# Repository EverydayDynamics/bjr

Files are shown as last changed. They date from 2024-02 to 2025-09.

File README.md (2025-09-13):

# bjr
A Ball Juggling Robot's repository

## Getting started

### firmware build and flashing

install rust on you computer
```
curl --proto '=https' --tlsv1.2 -sSf https://sh.rustup.rs | sh
```
Install the target toolchain

```
rustup target add thumbv7em-none-eabihf
```

Install probe-rs
```
curl --proto '=https' --tlsv1.2 -LsSf https://github.com/probe-rs/probe-rs/releases/latest/download/probe-rs-tools-installer.sh | sh
```
Download and install jlink tools from here
https://www.segger.com/downloads/jlink/
Restart your shell
Change directory to the main software
```
cd software/central_control_firmware
```

Build the firmware with:
```
cargo embed --bin main_app --release 
```
### telemetry visualizer build
Change directory to the visualizer
```
cd software/telemetry_visualizer
```

Build the visualizer with:
```
cargo embed --bin main_app --release 
```

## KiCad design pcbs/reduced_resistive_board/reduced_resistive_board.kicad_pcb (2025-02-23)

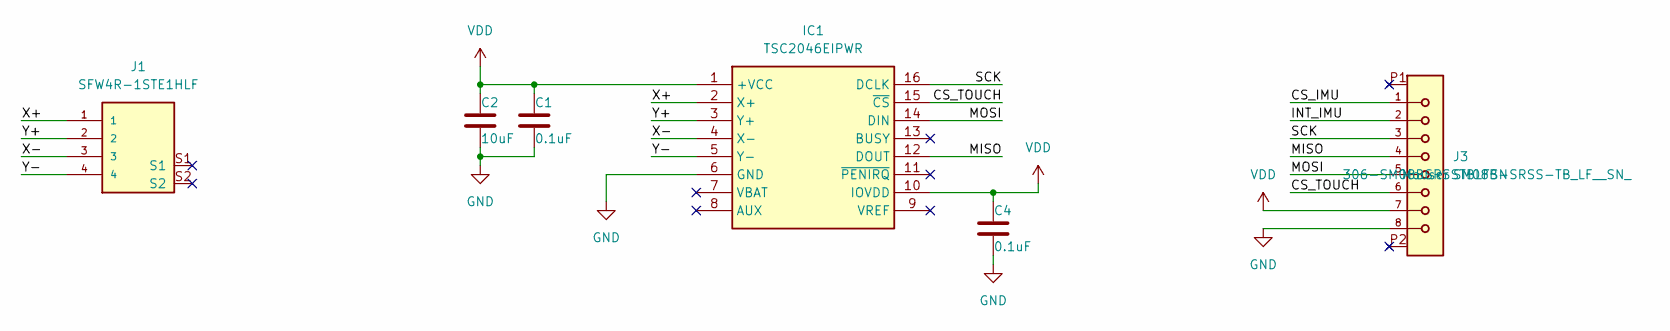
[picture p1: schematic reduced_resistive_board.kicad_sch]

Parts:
C1, C4: 0.1uF; C_0805_2012Metric_Pad1.18x1.45mm_HandSolder
C2: 10uF; C_0805_2012Metric_Pad1.18x1.45mm_HandSolder
IC1: TSC2046EIPWR; SOP65P640X120-16N; Mouser Part Number 595-TSC2046EIPWR
J1: SFW4R-1STE1HLF; AMPHENOL_SFW4R-1STE1HLF; PARTREV B
J3: SM08B-SRSS-TB_LF__SN_; JST_SM08B-SRSS-TB_LF__SN_

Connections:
/CS_IMU: J3.1
/CS_TOUCH: IC1.15 (~CS), J3.6
/INT_IMU: J3.2
/MISO: IC1.12 (DOUT), J3.4
/MOSI: IC1.14 (DIN), J3.5
/SCK: IC1.16 (DCLK), J3.3
/X+: IC1.2 (X+), J1.1
/X-: IC1.4 (X-), J1.3
/Y+: IC1.3 (Y+), J1.2
/Y-: IC1.5 (Y-), J1.4
GND: C1.2, C2.2, C4.2, IC1.6 (GND), J3.8
VDD: C1.1, C2.1, C4.1, IC1.1 (+VCC), IC1.10 (IOVDD), J3.7

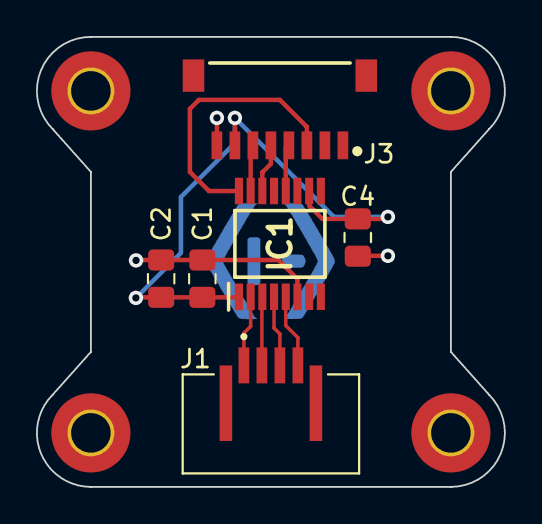
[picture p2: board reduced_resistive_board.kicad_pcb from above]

Board: 2 copper layers, 26.0 x 25.0 mm, 6 parts (0 on the bottom side), 10 nets.

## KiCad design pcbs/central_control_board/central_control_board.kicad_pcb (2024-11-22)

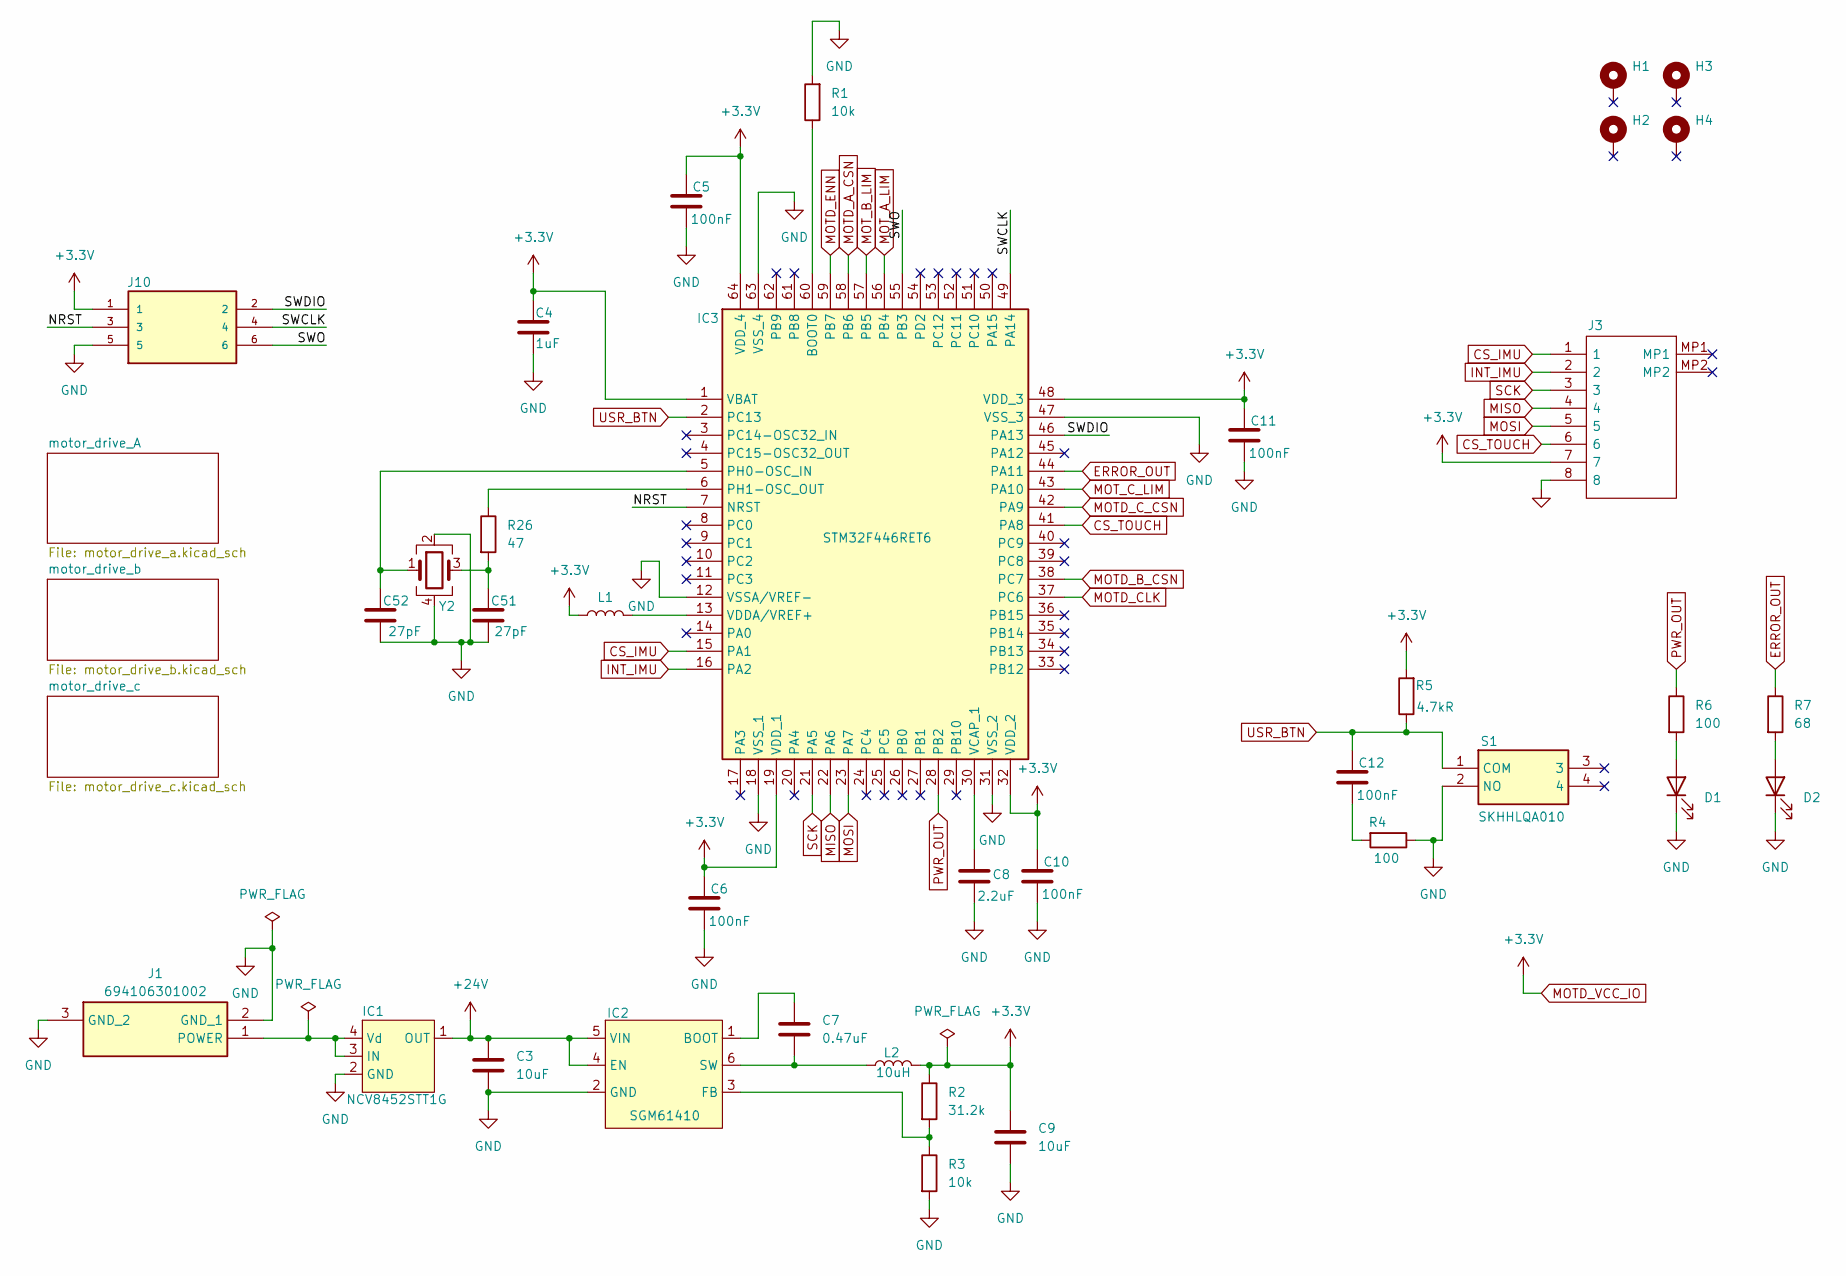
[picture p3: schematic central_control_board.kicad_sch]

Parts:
C3, C9: 10uF; C_1206_3216Metric_Pad1.33x1.80mm_HandSolder
C4: 1uF; C_0603_1608Metric_Pad1.08x0.95mm_HandSolder
C5, C6, C10, C11, C12: 100nF; C_0603_1608Metric_Pad1.08x0.95mm_HandSolder
C7: 0.47uF; C_0603_1608Metric_Pad1.08x0.95mm_HandSolder
C8: 2.2uF; C_0603_1608Metric_Pad1.08x0.95mm_HandSolder
C51, C52: 27pF; C_0603_1608Metric_Pad1.08x0.95mm_HandSolder
D1: LED red; LED_0603_1608Metric_Pad1.05x0.95mm_HandSolder
D2: LED white; LED_0603_1608Metric_Pad1.05x0.95mm_HandSolder
H1, H2, H3, H4: MountingHole_Pad; MountingHole_2.7mm_M2.5_ISO14580_Pad
IC1: NCV8452STT1G; SOT-223
IC2: SGM61410; SOT-23-6; mfg_part_num SGM61410XN6G/TR
IC3: STM32F446RET6; LQFP64-10x10mm; Manufacturer_Part_Number STM32F446RET6
J1: 694106301002; Manufacturer_Part_Number 694106301002
J3: BM08B-SRSS-TBT_LF__SN_; BM08BSRSSTBTLFSN; Manufacturer_Part_Number BM08B-SRSS-TBT(LF)(SN)
J10: 8.06.16_J-LINK_6-PIN_NEEDLE_ADAPTER; SEGGER_8.06.16_J-LINK_6-PIN_NEEDLE_ADAPTER; PARTREV A
L1: bead; L_1206_3216Metric
L2: 10uH; LQH3NPN100MJRL
R1, R3: 10k; R_0603_1608Metric_Pad0.98x0.95mm_HandSolder
R2: 31.2k; R_0603_1608Metric_Pad0.98x0.95mm_HandSolder
R4, R6: 100; R_0603_1608Metric_Pad0.98x0.95mm_HandSolder
R5: 4.7kR; R_0603_1608Metric_Pad0.98x0.95mm_HandSolder
R7: 68; R_0603_1608Metric_Pad0.98x0.95mm_HandSolder
R26: 47; R_0603_1608Metric_Pad0.98x0.95mm_HandSolder
S1: SKHHLQA010
Y2: Crystal_GND24; Crystal_SMD_5032-4Pin_5.0x3.2mm

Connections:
+24V: C3.1, IC1.1 (OUT), IC2.4 (EN), IC2.5 (VIN); also elsewhere on the board
/NRST: IC3.7 (NRST), J10.3
/SWCLK: IC3.49 (PA14), J10.4
/SWDIO: IC3.46 (PA13), J10.2
/SWO: IC3.55 (PB3), J10.6
CS_IMU: IC3.15 (PA1), J3.1
CS_TOUCH: IC3.41 (PA8), J3.6
ERROR_OUT: IC3.44 (PA11), R7.1
GND: C3.2, C4.1, C5.2, C6.2, C8.1, C9.2, C10.2, C11.2, C51.2, C52.2, D1.1 (K), D2.1 (K), IC1.2 (GND), IC2.2 (GND), IC3.12 (VSSA/VREF-), IC3.18 (VSS_1), IC3.31 (VSS_2), IC3.47 (VSS_3), IC3.63 (VSS_4), J1.2 (GND_1), J1.3 (GND_2), J3.8, J10.5, R1.2, R3.2, R4.1, S1.2 (NO), Y2.2, Y2.4; also elsewhere on the board
INT_IMU: IC3.16 (PA2), J3.2
MISO: IC3.22 (PA6), J3.4; also elsewhere on the board
MOSI: IC3.23 (PA7), J3.5; also elsewhere on the board
MOTD_A_CSN: IC3.58 (PB6); also elsewhere on the board
MOTD_B_CSN: IC3.38 (PC7); also elsewhere on the board
MOTD_CLK: IC3.37 (PC6); also elsewhere on the board
MOTD_C_CSN: IC3.42 (PA9); also elsewhere on the board
MOTD_ENN: IC3.59 (PB7); also elsewhere on the board
MOTD_VCC_IO: C4.2, C5.1, C6.1, C9.1, C10.1, C11.1, IC3.1 (VBAT), IC3.19 (VDD_1), IC3.32 (VDD_2), IC3.48 (VDD_3), IC3.64 (VDD_4), J3.7, J10.1, L1.1, L2.2, R2.1, R5.2; also elsewhere on the board
MOT_A_LIM: IC3.56 (PB4); also elsewhere on the board
MOT_B_LIM: IC3.57 (PB5); also elsewhere on the board
MOT_C_LIM: IC3.43 (PA10); also elsewhere on the board
unnamed: C12.2, R4.2
unnamed: C51.1, R26.2, Y2.3
unnamed: D1.2 (A), R6.2
unnamed: D2.2 (A), R7.2
unnamed: IC1.3 (IN), IC1.4 (Vd), J1.1 (POWER)
unnamed: C7.1, IC2.1 (BOOT)
unnamed: IC2.3 (FB), R2.2, R3.1
unnamed: C7.2, IC2.6 (SW), L2.1
unnamed: IC3.60 (BOOT0), R1.1
unnamed: C52.1, IC3.5 (PH0-OSC_IN), Y2.1
unnamed: IC3.6 (PH1-OSC_OUT), R26.1
unnamed: C8.2, IC3.30 (VCAP_1)
unnamed: IC3.13 (VDDA/VREF+), L1.2
PWR_OUT: IC3.28 (PB2), R6.1
SCK: IC3.21 (PA5), J3.3; also elsewhere on the board
USR_BTN: C12.1, IC3.2 (PC13), R5.1, S1.1 (COM)

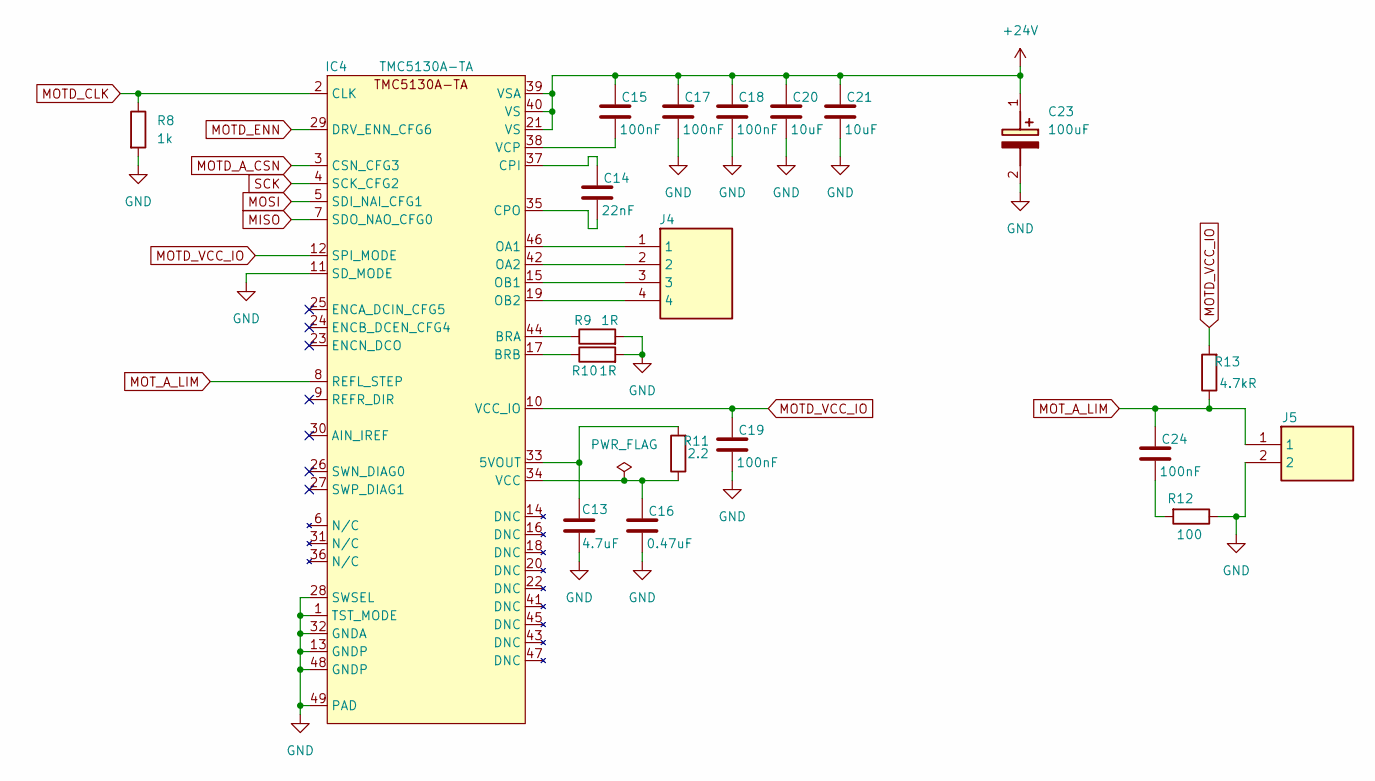
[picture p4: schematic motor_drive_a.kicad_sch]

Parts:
C13: 4.7uF; C_0603_1608Metric_Pad1.08x0.95mm_HandSolder
C14: 22nF; C_0603_1608Metric_Pad1.08x0.95mm_HandSolder
C15, C17, C18, C19, C24: 100nF; C_0603_1608Metric_Pad1.08x0.95mm_HandSolder
C16: 0.47uF; C_0603_1608Metric_Pad1.08x0.95mm_HandSolder
C20, C21: 10uF; C_1206_3216Metric_Pad1.33x1.80mm_HandSolder
C23: 100uF; CAPPRD250W50D655H1250
IC4: TMC5130A-TA; TQFP-48-1EP_7x7mm_P0.5mm_EP5x5mm_ThermalVias
J4: B4B-ZR_LF__SN_; SHDR4W50P0X150_1X4_750X350X450P; Manufacturer_Part_Number B4B-ZR(LF)(SN)
J5: B2B-ZR_LF__SN_; SHDR2W50P0X150_1X2_450X350X450P; Manufacturer_Part_Number B2B-ZR(LF)(SN)
R8: 1k; R_0603_1608Metric_Pad0.98x0.95mm_HandSolder
R9, R10: 1R; R_1206_3216Metric_Pad1.30x1.75mm_HandSolder
R11: 2.2; R_0603_1608Metric_Pad0.98x0.95mm_HandSolder
R12: 100; R_0603_1608Metric_Pad0.98x0.95mm_HandSolder
R13: 4.7kR; R_0603_1608Metric_Pad0.98x0.95mm_HandSolder

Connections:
+24V: C15.1, C17.1, C18.1, C20.1, C21.1, C23.1 (+), IC4.21 (VS), IC4.39 (VSA), IC4.40 (VS); also elsewhere on the board
GND: C13.2, C16.2, C17.2, C18.2, C19.2, C20.2, C21.2, C23.2 (-), IC4.1 (TST_MODE), IC4.11 (SD_MODE), IC4.13 (GNDP), IC4.28 (SWSEL), IC4.32 (GNDA), IC4.48 (GNDP), IC4.49 (PAD), J5.2, R8.2, R9.2, R10.2, R12.1; also elsewhere on the board
MISO: IC4.7 (SDO_NAO_CFG0); also elsewhere on the board
MOSI: IC4.5 (SDI_NAI_CFG1); also elsewhere on the board
MOTD_A_CSN: IC4.3 (CSN_CFG3); also elsewhere on the board
MOTD_CLK: IC4.2 (CLK), R8.1; also elsewhere on the board
MOTD_ENN: IC4.29 (DRV_ENN_CFG6); also elsewhere on the board
MOTD_VCC_IO: C19.1, IC4.10 (VCC_IO), IC4.12 (SPI_MODE), R13.2; also elsewhere on the board
MOT_A_LIM: C24.1, IC4.8 (REFL_STEP), J5.1, R13.1; also elsewhere on the board
unnamed: C24.2, R12.2
unnamed: C13.1, IC4.33 (5VOUT), R11.2
unnamed: IC4.44 (BRA), R9.1
unnamed: IC4.17 (BRB), R10.1
unnamed: C14.1, IC4.37 (CPI)
unnamed: C14.2, IC4.35 (CPO)
unnamed: IC4.46 (OA1), J4.1
unnamed: IC4.42 (OA2), J4.2
unnamed: IC4.15 (OB1), J4.3
unnamed: IC4.19 (OB2), J4.4
unnamed: C16.1, IC4.34 (VCC), R11.1
unnamed: C15.2, IC4.38 (VCP)
SCK: IC4.4 (SCK_CFG2); also elsewhere on the board

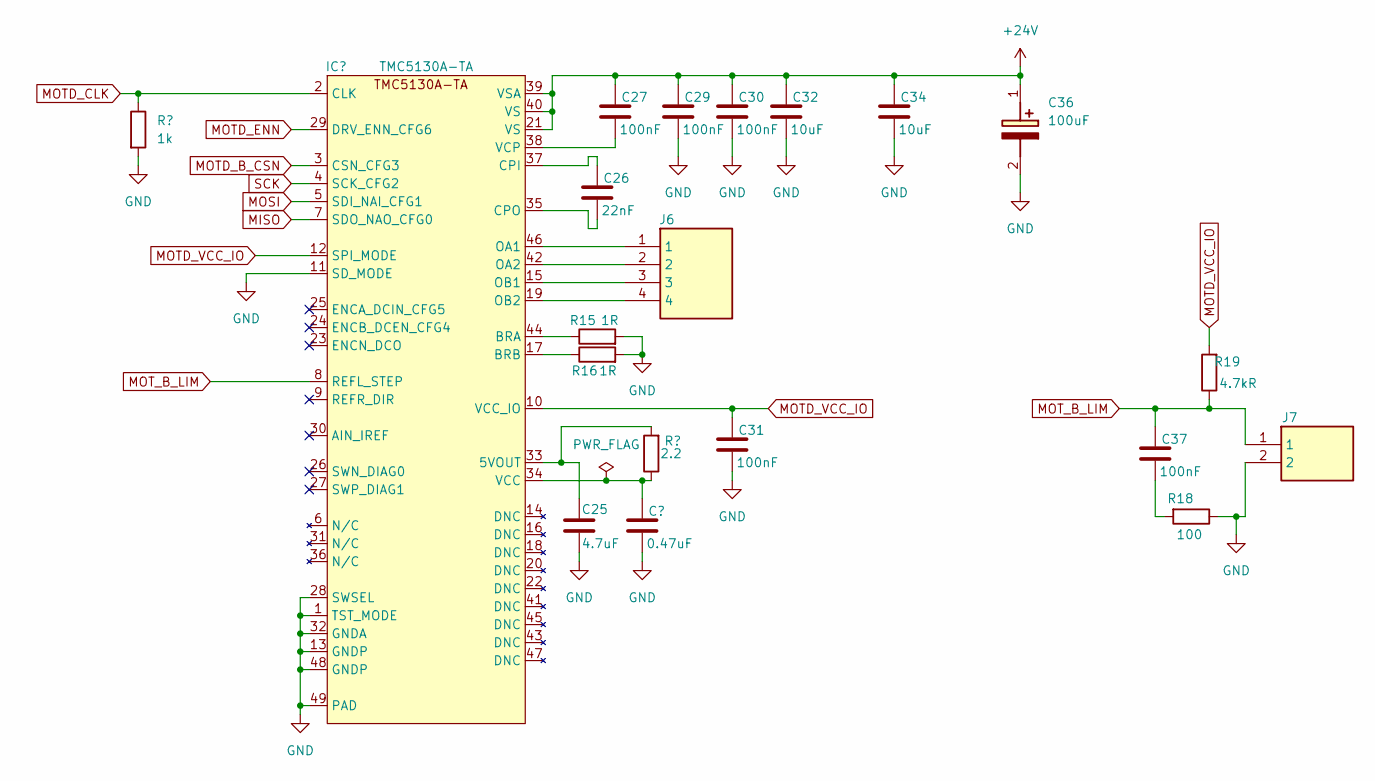
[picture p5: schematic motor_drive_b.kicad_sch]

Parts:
C25: 4.7uF; C_0603_1608Metric_Pad1.08x0.95mm_HandSolder
C26: 22nF; C_0603_1608Metric_Pad1.08x0.95mm_HandSolder
C27, C29, C30, C31, C37: 100nF; C_0603_1608Metric_Pad1.08x0.95mm_HandSolder
C28: 0.47uF; C_0603_1608Metric_Pad1.08x0.95mm_HandSolder
C32, C34: 10uF; C_1206_3216Metric_Pad1.33x1.80mm_HandSolder
C36: 100uF; CAPPRD250W50D655H1250
IC5: TMC5130A-TA; TQFP-48-1EP_7x7mm_P0.5mm_EP5x5mm_ThermalVias
J6: B4B-ZR_LF__SN_; SHDR4W50P0X150_1X4_750X350X450P; Manufacturer_Part_Number B4B-ZR(LF)(SN)
J7: B2B-ZR_LF__SN_; SHDR2W50P0X150_1X2_450X350X450P; Manufacturer_Part_Number B2B-ZR(LF)(SN)
R14: 1k; R_0603_1608Metric_Pad0.98x0.95mm_HandSolder
R15, R16: 1R; R_1206_3216Metric_Pad1.30x1.75mm_HandSolder
R17: 2.2; R_0603_1608Metric_Pad0.98x0.95mm_HandSolder
R18: 100; R_0603_1608Metric_Pad0.98x0.95mm_HandSolder
R19: 4.7kR; R_0603_1608Metric_Pad0.98x0.95mm_HandSolder

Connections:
+24V: C27.1, C29.1, C30.1, C32.1, C34.1, C36.1 (+), IC5.21 (VS), IC5.39 (VSA), IC5.40 (VS); also elsewhere on the board
GND: C25.2, C28.2, C29.2, C30.2, C31.2, C32.2, C34.2, C36.2 (-), IC5.1 (TST_MODE), IC5.11 (SD_MODE), IC5.13 (GNDP), IC5.28 (SWSEL), IC5.32 (GNDA), IC5.48 (GNDP), IC5.49 (PAD), J7.2, R14.2, R15.2, R16.2, R18.1; also elsewhere on the board
MISO: IC5.7 (SDO_NAO_CFG0); also elsewhere on the board
MOSI: IC5.5 (SDI_NAI_CFG1); also elsewhere on the board
MOTD_B_CSN: IC5.3 (CSN_CFG3); also elsewhere on the board
MOTD_CLK: IC5.2 (CLK), R14.1; also elsewhere on the board
MOTD_ENN: IC5.29 (DRV_ENN_CFG6); also elsewhere on the board
MOTD_VCC_IO: C31.1, IC5.10 (VCC_IO), IC5.12 (SPI_MODE), R19.2; also elsewhere on the board
MOT_B_LIM: C37.1, IC5.8 (REFL_STEP), J7.1, R19.1; also elsewhere on the board
unnamed: C37.2, R18.2
unnamed: C25.1, IC5.33 (5VOUT), R17.2
unnamed: IC5.44 (BRA), R15.1
unnamed: IC5.17 (BRB), R16.1
unnamed: C26.1, IC5.37 (CPI)
unnamed: C26.2, IC5.35 (CPO)
unnamed: IC5.46 (OA1), J6.1
unnamed: IC5.42 (OA2), J6.2
unnamed: IC5.15 (OB1), J6.3
unnamed: IC5.19 (OB2), J6.4
unnamed: C28.1, IC5.34 (VCC), R17.1
unnamed: C27.2, IC5.38 (VCP)
SCK: IC5.4 (SCK_CFG2); also elsewhere on the board

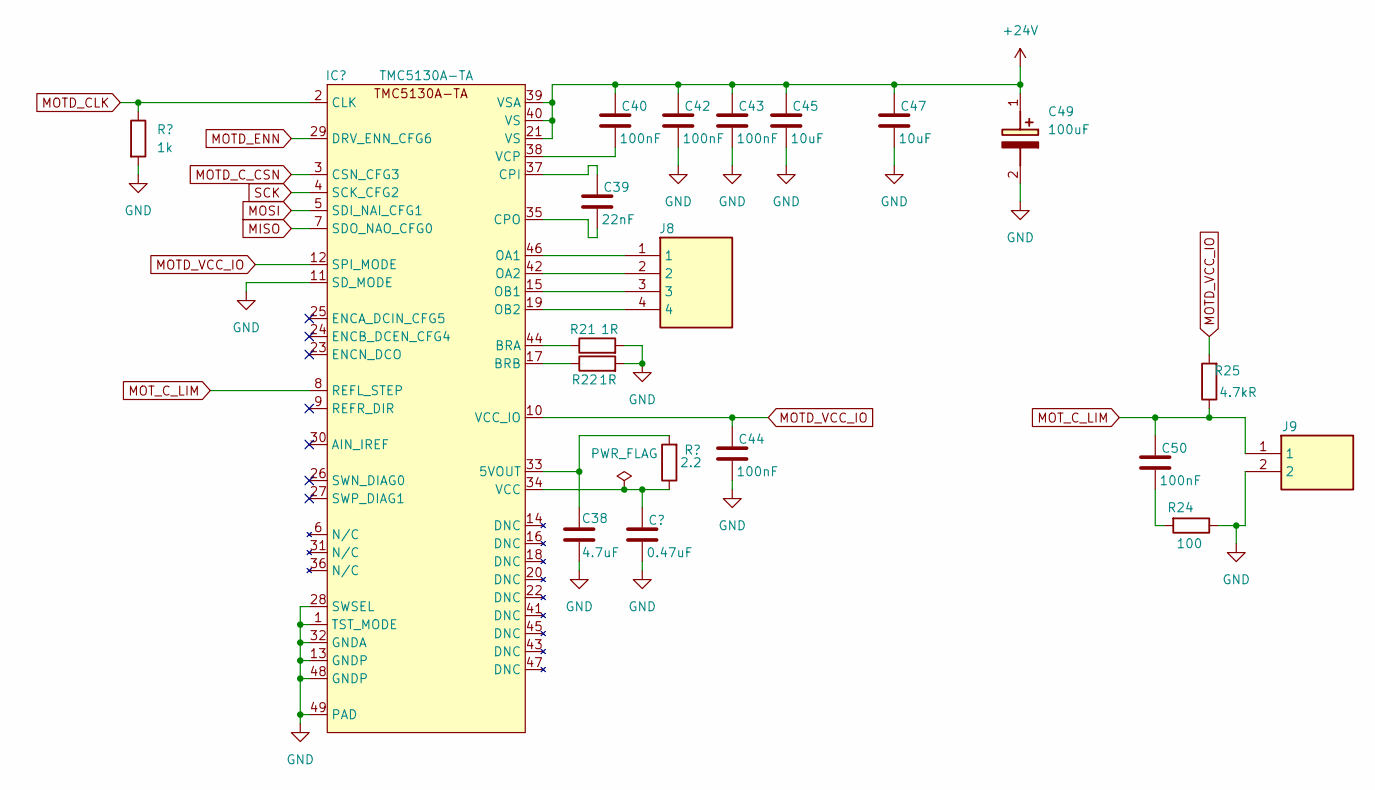
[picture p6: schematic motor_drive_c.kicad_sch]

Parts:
C38: 4.7uF; C_0603_1608Metric_Pad1.08x0.95mm_HandSolder
C39: 22nF; C_0603_1608Metric_Pad1.08x0.95mm_HandSolder
C40, C42, C43, C44, C50: 100nF; C_0603_1608Metric_Pad1.08x0.95mm_HandSolder
C41: 0.47uF; C_0603_1608Metric_Pad1.08x0.95mm_HandSolder
C45, C47: 10uF; C_1206_3216Metric_Pad1.33x1.80mm_HandSolder
C49: 100uF; CAPPRD250W50D655H1250
IC6: TMC5130A-TA; TQFP-48-1EP_7x7mm_P0.5mm_EP5x5mm_ThermalVias
J8: B4B-ZR_LF__SN_; SHDR4W50P0X150_1X4_750X350X450P; Manufacturer_Part_Number B4B-ZR(LF)(SN)
J9: B2B-ZR_LF__SN_; SHDR2W50P0X150_1X2_450X350X450P; Manufacturer_Part_Number B2B-ZR(LF)(SN)
R20: 1k; R_0603_1608Metric_Pad0.98x0.95mm_HandSolder
R21, R22: 1R; R_1206_3216Metric_Pad1.30x1.75mm_HandSolder
R23: 2.2; R_0603_1608Metric_Pad0.98x0.95mm_HandSolder
R24: 100; R_0603_1608Metric_Pad0.98x0.95mm_HandSolder
R25: 4.7kR; R_0603_1608Metric_Pad0.98x0.95mm_HandSolder

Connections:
+24V: C40.1, C42.1, C43.1, C45.1, C47.1, C49.1 (+), IC6.21 (VS), IC6.39 (VSA), IC6.40 (VS); also elsewhere on the board
GND: C38.2, C41.2, C42.2, C43.2, C44.2, C45.2, C47.2, C49.2 (-), IC6.1 (TST_MODE), IC6.11 (SD_MODE), IC6.13 (GNDP), IC6.28 (SWSEL), IC6.32 (GNDA), IC6.48 (GNDP), IC6.49 (PAD), J9.2, R20.2, R21.2, R22.2, R24.1; also elsewhere on the board
MISO: IC6.7 (SDO_NAO_CFG0); also elsewhere on the board
MOSI: IC6.5 (SDI_NAI_CFG1); also elsewhere on the board
MOTD_CLK: IC6.2 (CLK), R20.1; also elsewhere on the board
MOTD_C_CSN: IC6.3 (CSN_CFG3); also elsewhere on the board
MOTD_ENN: IC6.29 (DRV_ENN_CFG6); also elsewhere on the board
MOTD_VCC_IO: C44.1, IC6.10 (VCC_IO), IC6.12 (SPI_MODE), R25.2; also elsewhere on the board
MOT_C_LIM: C50.1, IC6.8 (REFL_STEP), J9.1, R25.1; also elsewhere on the board
unnamed: C50.2, R24.2
unnamed: C38.1, IC6.33 (5VOUT), R23.2
unnamed: IC6.44 (BRA), R21.1
unnamed: IC6.17 (BRB), R22.1
unnamed: C39.1, IC6.37 (CPI)
unnamed: C39.2, IC6.35 (CPO)
unnamed: IC6.46 (OA1), J8.1
unnamed: IC6.42 (OA2), J8.2
unnamed: IC6.15 (OB1), J8.3
unnamed: IC6.19 (OB2), J8.4
unnamed: C41.1, IC6.34 (VCC), R23.1
unnamed: C40.2, IC6.38 (VCP)
SCK: IC6.4 (SCK_CFG2); also elsewhere on the board

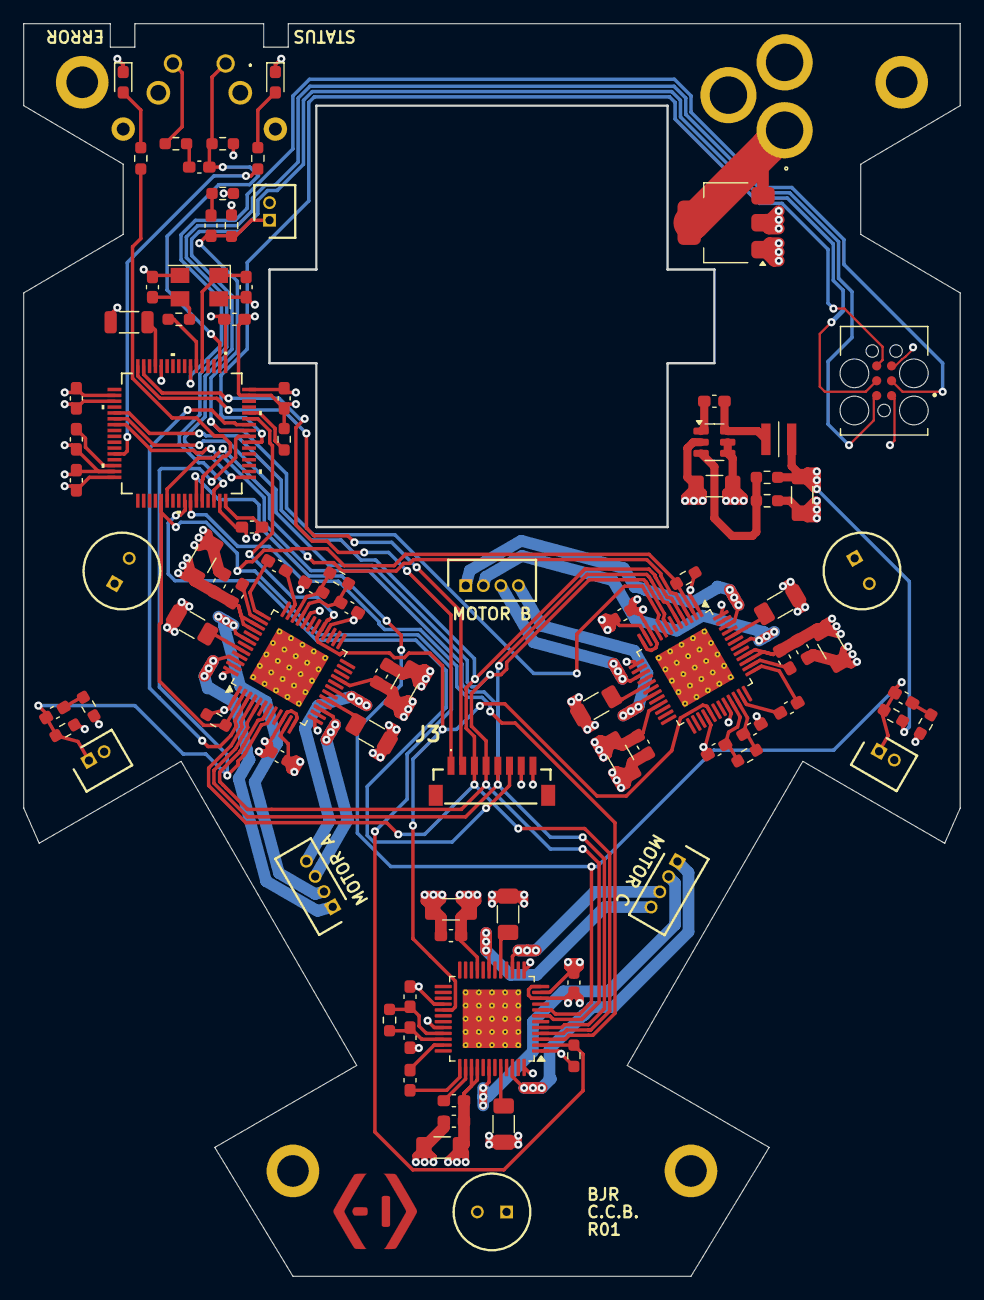
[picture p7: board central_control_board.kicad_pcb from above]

Board: 4 copper layers, 80.0 x 107.0 mm, 96 parts (0 on the bottom side), 73 nets.

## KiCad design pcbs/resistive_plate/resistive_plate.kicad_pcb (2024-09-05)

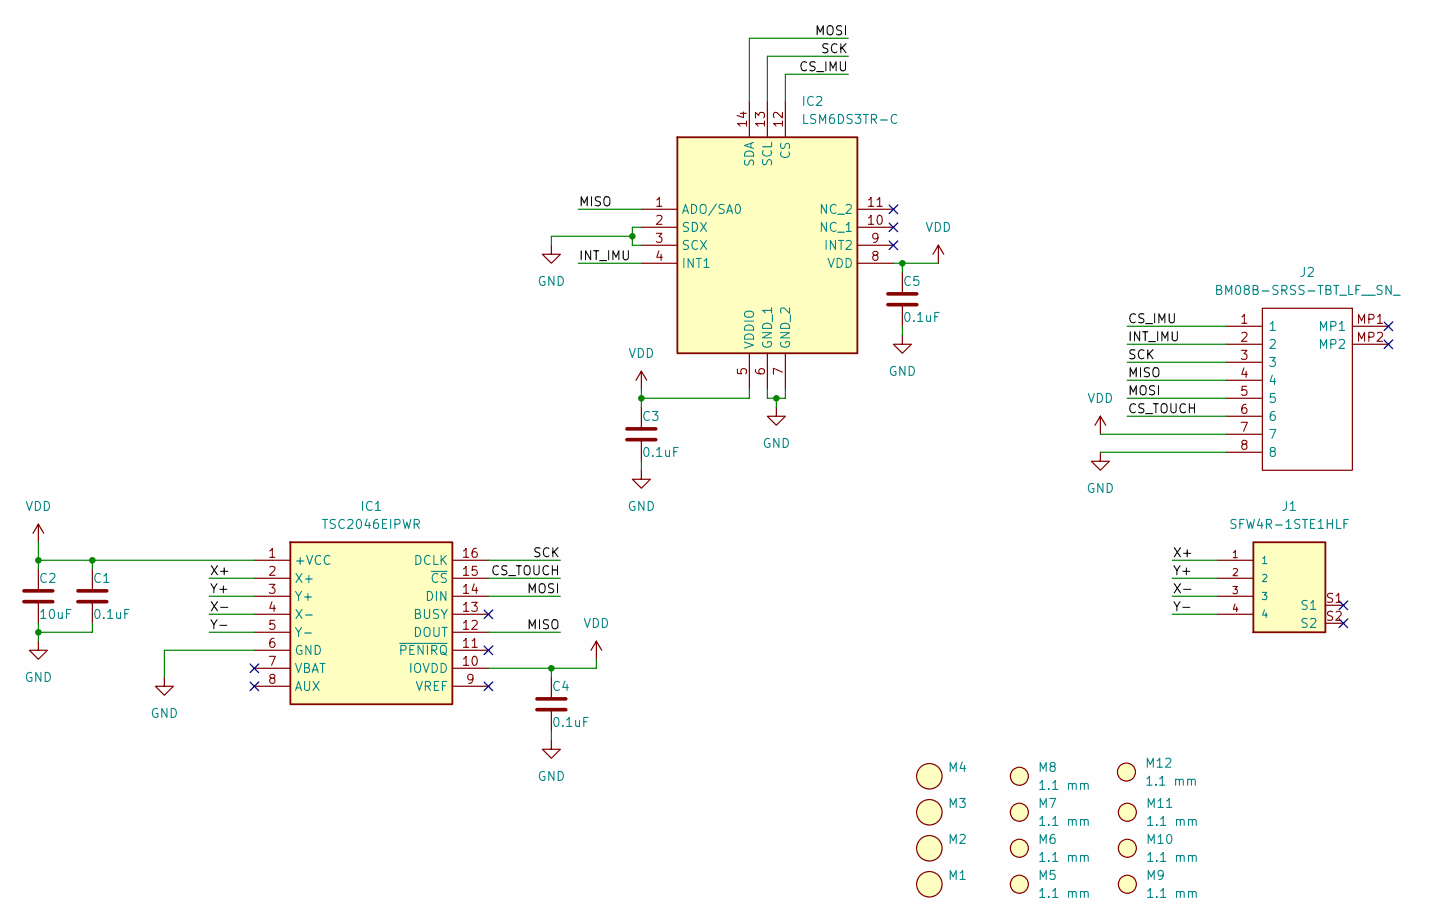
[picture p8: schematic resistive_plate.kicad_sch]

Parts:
C1, C3, C4, C5: 0.1uF; C_0805_2012Metric_Pad1.18x1.45mm_HandSolder
C2: 10uF; C_0805_2012Metric_Pad1.18x1.45mm_HandSolder
IC1: TSC2046EIPWR; SOP65P640X120-16N; Mouser Part Number 595-TSC2046EIPWR
IC2: LSM6DS3TR-C; LGA-14_2.5X3X0.86_; Mouser Part Number 511-LSM6DS3TR-C
J1: SFW4R-1STE1HLF; AMPHENOL_SFW4R-1STE1HLF; PARTREV B
J2: BM08B-SRSS-TBT_LF__SN_; BM08BSRSSTBTLFSN; Manufacturer_Part_Number BM08B-SRSS-TBT(LF)(SN)
M1, M2, M3, M4: WURTH ELEKTRONIK 9774010151R
M5, M6, M7, M8, M9, M10, M11, M12: 1.1 mm; Mounting hole 1.1 mm

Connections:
/CS_IMU: IC2.12 (CS), J2.1
/CS_TOUCH: IC1.15 (~CS), J2.6
/INT_IMU: IC2.4 (INT1), J2.2
/MISO: IC1.12 (DOUT), IC2.1 (ADO/SA0), J2.4
/MOSI: IC1.14 (DIN), IC2.14 (SDA), J2.5
/SCK: IC1.16 (DCLK), IC2.13 (SCL), J2.3
/X+: IC1.2 (X+), J1.1
/X-: IC1.4 (X-), J1.3
/Y+: IC1.3 (Y+), J1.2
/Y-: IC1.5 (Y-), J1.4
GND: C1.2, C2.2, C3.2, C4.2, C5.2, IC1.6 (GND), IC2.2 (SDX), IC2.3 (SCX), IC2.6 (GND_1), IC2.7 (GND_2), J2.8
VDD: C1.1, C2.1, C3.1, C4.1, C5.1, IC1.1 (+VCC), IC1.10 (IOVDD), IC2.5 (VDDIO), IC2.8 (VDD), J2.7

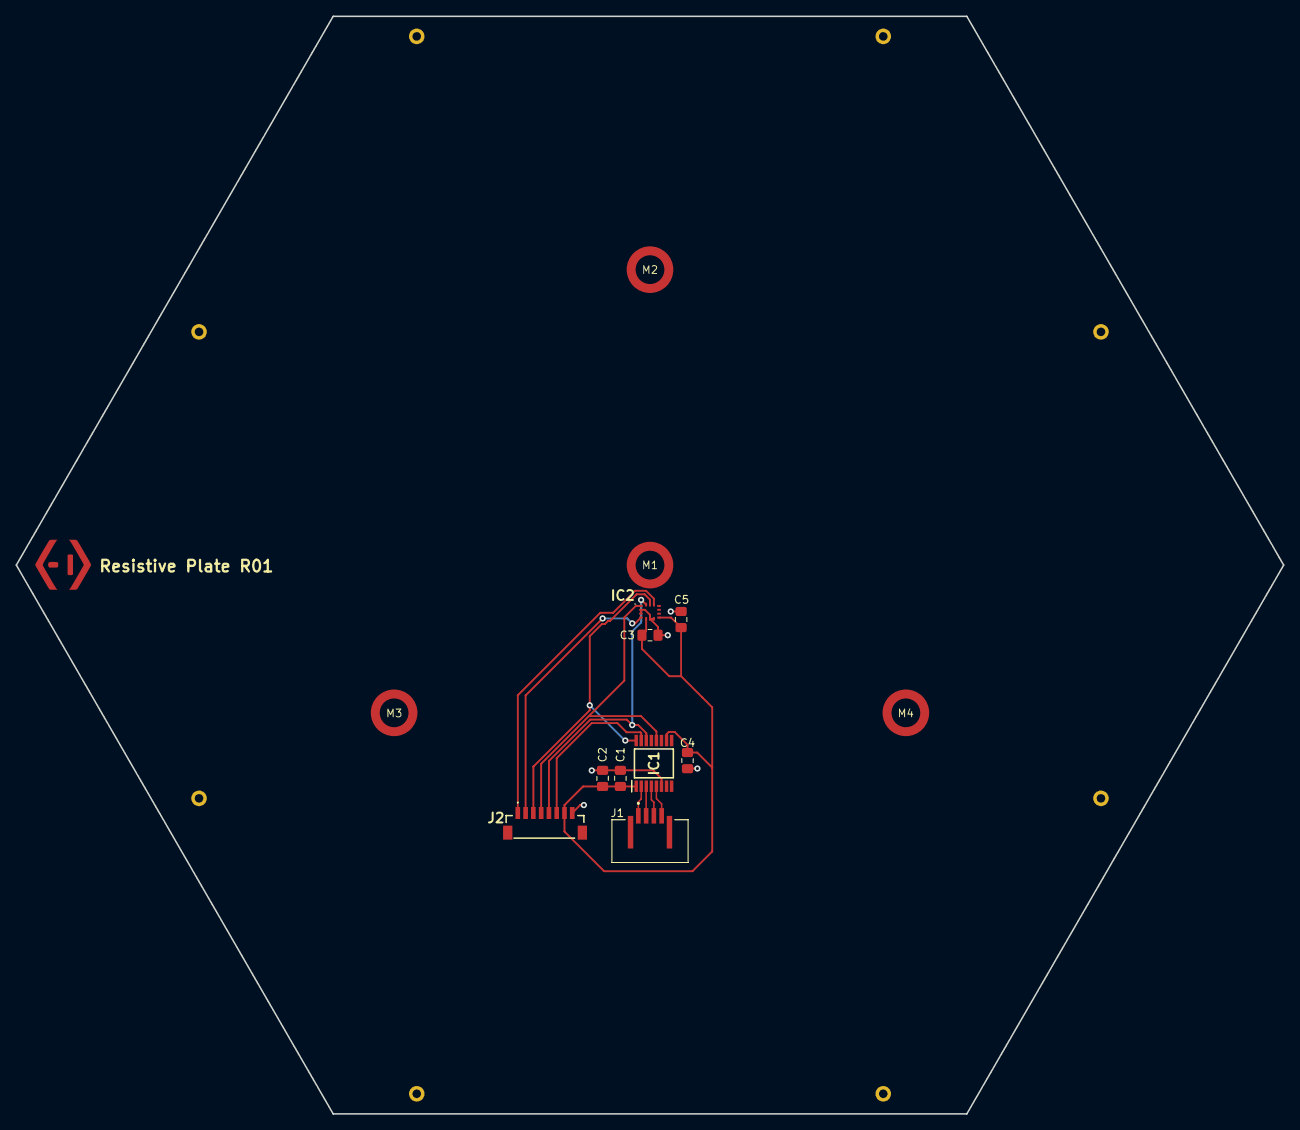
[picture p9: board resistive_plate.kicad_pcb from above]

Board: 2 copper layers, 163.0 x 141.2 mm, 21 parts (0 on the bottom side), 12 nets.

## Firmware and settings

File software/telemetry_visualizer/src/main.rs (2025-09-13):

use eframe::{egui, HardwareAcceleration};
use eframe::egui::Theme;
use egui_plot::{Legend, Line, Plot, PlotBounds, PlotPoint, PlotPoints, Points, Arrows};
use serde::{Deserialize, Serialize};
use std::collections::VecDeque;
use std::error::Error;
use std::io::Read;
use std::net::TcpListener;
use std::sync::{Arc, Mutex};
use std::thread;
use eframe::egui::{Vec2b, ViewportBuilder};
use telemetry_interface::{TelemetryData, TelemetryPacket};
use strum::{EnumCount, VariantNames};
use rfd::FileDialog;
use csv::Writer;
use std::fs::File;

const MAX_POINTS: usize = 1000;

struct TelemetryHolder {
    pub data: VecDeque<TelemetryPacket>,
}

impl TelemetryHolder {
    fn new() -> Self {
        TelemetryHolder {
            data: VecDeque::with_capacity(MAX_POINTS)
        }
    }

    fn add_packet(&mut self, packet: TelemetryPacket) {
        if self.data.len() == MAX_POINTS {
            self.data.pop_front();
        }
        self.data.push_back(packet)
    }
}

struct TelemetryApp {
    telemetry_data: Arc<Mutex<TelemetryHolder>>,
    lines: Vec<Vec<PlotPoint>>,
    line_visibility: [bool;TelemetryData::COUNT],
    reset_view: bool,
    update_view: bool,
    reset_ball_view: bool,
}
fn get_ball_position_and_velocity(telemetry_data: &TelemetryHolder) -> Option<(PlotPoint, PlotPoint)> {
    let latest_packet = telemetry_data.data.back()?;

    let ball_x_pos_idx = TelemetryData::VARIANTS.iter().position(|&name| name == "BallXPos")?;
    let ball_y_pos_idx = TelemetryData::VARIANTS.iter().position(|&name| name == "BallYPos")?;
    let ball_x_vel_idx = TelemetryData::VARIANTS.iter().position(|&name| name == "BallXVel")?;
    let ball_y_vel_idx = TelemetryData::VARIANTS.iter().position(|&name| name == "BallYVel")?;

    let ball_x_pos = latest_packet.data[ball_x_pos_idx]?.get_printable_value();
    let ball_y_pos = latest_packet.data[ball_y_pos_idx]?.get_printable_value();
    let ball_x_vel = latest_packet.data[ball_x_vel_idx]?.get_printable_value();
    let ball_y_vel = latest_packet.data[ball_y_vel_idx]?.get_printable_value();

    Some((
        PlotPoint::new(ball_x_pos, ball_y_pos),
        PlotPoint::new(ball_x_vel, ball_y_vel)
    ))
}

impl TelemetryApp {
    fn new(telemetry_data: Arc<Mutex<TelemetryHolder>>) -> Self {
        Self {
            telemetry_data,
            line_visibility: [false;TelemetryData::COUNT],
            reset_view: false,
            update_view: true,
            reset_ball_view: false,
            lines: std::iter::repeat(Vec::with_capacity(MAX_POINTS)).take(TelemetryData::COUNT).collect(),
        }
    }

    fn get_update_button_text(&self) -> &'static str {
        if self.update_view {
            "Pause"
        } else {
            "Run"
        }
    }

    fn update_button_clicked(&mut self){
        if self.update_view {
            self.update_view = false;
        } else {
            self.update_view = true;
        }
    }

    fn flush_buffer(&mut self){
        let mut telemetry_data = self.telemetry_data.lock().unwrap();
        telemetry_data.data.clear();
    }

    fn export_data(&mut self) {
        if let Some(path) = FileDialog::new()
            .add_filter("CSV file", &["csv"])
            .set_file_name("data_export.csv")
            .save_file()
        {
            // Open file
            let file = File::create(path).unwrap();
            let mut wtr = Writer::from_writer(file);

            // Write header
            let mut record:[String;27] = [const{String::new()};27];
            record[0] = "Packet ID".to_string();
            record[1] = "Timestamp [s]".to_string();
            let mut idx = 2;
            for field_name in TelemetryData::VARIANTS {
                record[idx]=field_name.to_string();
                idx+=1;
            }
            wtr.write_record(&record).unwrap();

            // Write data rows
            let telemetry_data = self.telemetry_data.lock().unwrap();
            for packet in &telemetry_data.data {
                let mut record:[String;27] = [const{String::new()};27];
                record[0] = packet.packet_id.to_string();
                record[1] = packet.timestamp.to_string();
                let mut idx = 2;
                for data in packet.data{
                    if let Some(data) = data {
                        record[idx]=data.get_printable_value().to_string();
                    }
                    idx+=1;
                }
                wtr.write_record(&record).unwrap();
            }
            wtr.flush().unwrap();
        }
    }

}

impl eframe::App for TelemetryApp {
    fn update(&mut self, ctx: &egui::Context, _frame: &mut eframe::Frame) {
        egui::CentralPanel::default().show(ctx, |ui| {
            egui::SidePanel::left("checkbox_panel").show(ctx, |ui| {
                ui.heading("Line Visibility");
                ui.add_space(10.0);

                for (i, visible) in self.line_visibility.iter_mut().enumerate() {
                    ui.checkbox(visible, TelemetryData::VARIANTS[i]);
                }
                ui.add_space(20.0);

                if ui.button("Reset view").clicked() {
                    self.reset_view = true;
                }

                if ui.button("Reset ball view").clicked() {
                    self.reset_ball_view = true;
                }

                if ui.button(self.get_update_button_text()).clicked() {
                    self.update_button_clicked();
                }
                if ui.button("Flush").clicked() {
                    self.flush_buffer();
                }
                if ui.button("Export").clicked() {
                    self.export_data();
                }
            });

            let telemetry_data = self.telemetry_data.lock().unwrap();

            egui::CentralPanel::default().show(ctx, |ui| {
                ui.vertical(|ui| {
                    let max_time_plot_height = 400.0;
                    let time_plot_height = (ui.available_height() * 0.5).min(max_time_plot_height);
                    ui.allocate_ui_with_layout(
                        egui::vec2(ui.available_width(), time_plot_height),
                        egui::Layout::top_down(egui::Align::LEFT),
                        |ui| {
                            Plot::new("telemetry_plot")
                                .legend(Legend::default())
                                .show(ui, |plot_ui| {
                                    if self.update_view {
                                        self.lines = std::iter::repeat(Vec::with_capacity(crate::MAX_POINTS)).take(TelemetryData::COUNT).collect();
                                        for packet in &telemetry_data.data {
                                            let x = packet.timestamp as f64 / 1000000.0;
                                            for idx in 0..TelemetryData::COUNT {
                                                if self.line_visibility[idx] {
                                                    if let Some(data) = packet.data[idx] {
                                                        self.lines[idx].push(PlotPoint { x, y: data.get_printable_value() })
                                                    }
                                                }
                                            }
                                        }
                                    }
                                    for (idx, line) in self.lines.iter().enumerate() {
                                        if self.line_visibility[idx] {
                                            plot_ui.line(Line::new("", PlotPoints::Owned(line.clone()) ).name(TelemetryData::VARIANTS[idx]));
                                        }
                                    }
                                    if self.reset_view{
                                        plot_ui.set_auto_bounds(Vec2b::new(true,true));
                                        self.reset_view = false;
                                    }
                                });
                        }
                    );

                    ui.separator();

                    let available_size = ui.available_size();
                    let square_size = available_size.x.min(available_size.y);
                    // Second plot - Ball position and velocity
                    ui.allocate_ui_with_layout(
                        egui::vec2(square_size, square_size),
                        egui::Layout::top_down(egui::Align::LEFT),
                        |ui| {
                            ui.label("Ball Position & Velocity");
                            Plot::new("ball_plot")
                                .legend(Legend::default())
                                .view_aspect(1.0)
                                .data_aspect(1.0)
                                .show(ui, |plot_ui| {
                                    if let Some((position, velocity)) = get_ball_position_and_velocity(&telemetry_data) {
                                        // Draw the ball position as a point
                                        plot_ui.points(
                                            Points::new("Ball Position", PlotPoints::Owned(vec![position]))
                                                .radius(5.0)
                                                .color(egui::Color32::RED)
                                        );

                                        // Draw the velocity vector as an arrow
                                        let arrow_end = PlotPoint::new(
                                            position.x + velocity.x * 0.1, // Scale the velocity vector for visibility
                                            position.y + velocity.y * 0.1
                                        );

                                        plot_ui.arrows(
                                            Arrows::new("", PlotPoints::Owned(vec![position]), PlotPoints::Owned(vec![arrow_end]))
                                                .name("Ball Velocity")
                                                .color(egui::Color32::BLUE)
                                        );

                                        // Draw a trajectory trail (last few positions)
                                        let trail_points: Vec<PlotPoint> = telemetry_data.data
                                            .iter()
                                            .rev()
                                            .take(50) // Show last 50 positions
                                            .filter_map(|packet| {
                                                let ball_x_pos_idx = TelemetryData::VARIANTS.iter().position(|&name| name == "BallXPos")?;
                                                let ball_y_pos_idx = TelemetryData::VARIANTS.iter().position(|&name| name == "BallYPos")?;
                                                let x = packet.data[ball_x_pos_idx]?.get_printable_value();
                                                let y = packet.data[ball_y_pos_idx]?.get_printable_value();
                                                Some(PlotPoint::new(x, y))
                                            })
                                            .collect();

                                        if !trail_points.is_empty() {
                                            plot_ui.line(
                                                Line::new("", PlotPoints::Owned(trail_points))
                                                    .name("Ball Trail")
                                                    .color(egui::Color32::GRAY)
                                                    .width(1.0)
                                            );
                                        }
                                    }

                                    if self.reset_ball_view {
                                        plot_ui.set_auto_bounds(Vec2b::new(true, true));
                                        self.reset_ball_view = false;
                                    }
                                });
                        }
                    );
                });
            });
        });

        // Request a repaint
        ctx.request_repaint();
    }
}

fn main() -> Result<(), Box<dyn Error>> {
    let telemetry_data = Arc::new(Mutex::new(TelemetryHolder::new()));
    let telemetry_data_clone = Arc::clone(&telemetry_data);

    // Spawn a thread to handle TCP connections
    thread::spawn(move || {
        let listener = TcpListener::bind("127.0.0.1:8080").unwrap();
        for mut maybe_stream in listener.incoming() {
            let mut stream = maybe_stream.unwrap();
            loop {
                let mut buffer = [0; 1024];
                match stream.read(&mut buffer) {
                    Ok(0) => break, // Connection closed
                    Ok(n) => {
                        if let Ok(packet) = postcard::from_bytes::<TelemetryPacket>(&buffer[..n]) {
                            let mut data = telemetry_data_clone.lock().unwrap();
                            data.add_packet(packet);
                        }
                    }
                    Err(_) => break, // Error occurred, break the loop
                }
            }
        }
        // close the socket server
        drop(listener);
    });

    let options = eframe::NativeOptions {
        viewport: ViewportBuilder::default().with_inner_size(egui::vec2(800.0, 800.0)), // Made taller for two plots
        vsync: false,
        multisampling: 0,
        depth_buffer: 0,
        stencil_buffer: 0,
        hardware_acceleration: HardwareAcceleration::Required,
        renderer: Default::default(),
        run_and_return: false,
        event_loop_builder: None,
        window_builder: None,
        shader_version: None,
        centered: false,
        persist_window: false,
        persistence_path: None,
        dithering: false,
    };

    eframe::run_native(
        "Telemetry Visualizer",
        options,
        Box::new(|_cc| Ok(Box::new(TelemetryApp::new(telemetry_data)))),
    )
        .map_err(|e| e.into())
}

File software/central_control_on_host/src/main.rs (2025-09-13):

use board_support_package::Board;
use application_builder::build_application;
use application_logic::app::menu_handler::MenuContext;
use embedded_time::duration::*;
use os_traits::TimeControl;
use std::thread;
use std::time::{Duration, Instant};
struct StdTimeControl {
    pub start_time: Instant,
}
impl StdTimeControl {
    pub fn new() -> StdTimeControl {
        StdTimeControl {
            start_time: Instant::now(),
        }
    }
}
impl TimeControl for StdTimeControl {
    fn get_tick(&self) -> u64 {
        (Instant::now() - self.start_time).as_micros() as u64
    }
}

fn main() {
    let std_time_control = StdTimeControl::new();
    let start_time = std_time_control.start_time;
    let mut board = Board::new();
    let mut menu_context = MenuContext::default();
    let mut logic_runner = build_application(&mut board, &mut menu_context, std_time_control);
    loop {
        let next_run = logic_runner.update();
        let time = (Instant::now() - start_time).as_micros() as u64;
        thread::sleep(Duration::from_micros(
            next_run.integer().saturating_sub(time),
        ));
    }
}

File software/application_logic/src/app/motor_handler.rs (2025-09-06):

use crate::app::consts::MOTOR_NUM;
use crate::app::control_primitives::KinState;
use crate::app::limits::{Limit, LimitError, MotorPosLimit, MotorVelLimit};
use crate::app::parameter_manager::{parameter_manager, MotorM2Ustep};
use crate::app::telemetry_handler::TelemetryBuilder;
use core::fmt::Display;
use core::fmt::Formatter;
use device_traits::{
    MotorInput, MotorMode, MotorState, StepperDeviceError, StepperMotorController,
};

#[derive(PartialEq, Copy, Clone, Default)]
pub enum ControlMode {
    #[default]
    Position,
    Velocity,
}
#[derive(Default, Copy, Clone)]
pub struct MotorStatus {
    pub limit_reached: bool,
    pub position_reached: bool,
    pub velocity_reached: bool,
    pub standstill: bool,
}
#[derive(PartialEq, Copy, Clone)]
pub enum MotorHandlerError {
    MotorError(StepperDeviceError, usize),
    MotorPositionLimitError(LimitError<f32>, usize),
    MotorVelocityLimitError(LimitError<f32>, usize),
    InputOverflow,
    MotorIdxOutOfRange(usize),
}

impl Display for MotorHandlerError {
    fn fmt(&self, f: &mut Formatter<'_>) -> core::fmt::Result {
        match self {
            MotorHandlerError::MotorError(e, idx) => {
                write!(f, "Motor Handler Motor error: {}, motor idx: {}", e, idx)
            }
            MotorHandlerError::MotorPositionLimitError(e, idx) => {
                write!(
                    f,
                    "MotorHandler Position limit error: {}, motor idx: {}",
                    e, idx
                )
            }
            MotorHandlerError::MotorVelocityLimitError(e, idx) => {
                write!(
                    f,
                    "MotorHandler Velocity limit error: {}, motor idx: {}",
                    e, idx
                )
            }
            MotorHandlerError::InputOverflow => {
                write!(f, "MotorHandler Input value overflow")
            }
            MotorHandlerError::MotorIdxOutOfRange(idx) => {
                write!(f, "MotorHandler Motor index ({}) out of range", idx)
            }
        }
    }
}
pub enum GenericMotor<MA, MB, MC>
where
    MA: StepperMotorController,
    MB: StepperMotorController,
    MC: StepperMotorController,
{
    MotorA(MA),
    MotorB(MB),
    MotorC(MC),
}
impl<MA, MB, MC> StepperMotorController for GenericMotor<MA, MB, MC>
where
    MA: StepperMotorController,
    MB: StepperMotorController,
    MC: StepperMotorController,
{
    fn set_inputs(&mut self, inputs: MotorInput) -> Result<(), StepperDeviceError> {
        match self {
            GenericMotor::MotorA(ma) => ma.set_inputs(inputs),
            GenericMotor::MotorB(mb) => mb.set_inputs(inputs),
            GenericMotor::MotorC(mc) => mc.set_inputs(inputs),
        }
    }

    fn get_state(&mut self) -> Result<MotorState, StepperDeviceError> {
        match self {
            GenericMotor::MotorA(ma) => ma.get_state(),
            GenericMotor::MotorB(mb) => mb.get_state(),
            GenericMotor::MotorC(mc) => mc.get_state(),
        }
    }

    fn set_position(&mut self, new_position: i32) -> Result<(), StepperDeviceError> {
        match self {
            GenericMotor::MotorA(ma) => ma.set_position(new_position),
            GenericMotor::MotorB(mb) => mb.set_position(new_position),
            GenericMotor::MotorC(mc) => mc.set_position(new_position),
        }
    }
    fn test_motion(&mut self) -> Result<(), StepperDeviceError> {
        match self {
            GenericMotor::MotorA(ma) => ma.test_motion(),
            GenericMotor::MotorB(mb) => mb.test_motion(),
            GenericMotor::MotorC(mc) => mc.test_motion(),
        }
    }
}
pub struct MotorHandler<MA, MB, MC>
where
    MA: StepperMotorController,
    MB: StepperMotorController,
    MC: StepperMotorController,
{
    motors: [GenericMotor<MA, MB, MC>; MOTOR_NUM],
    accel: [f32; MOTOR_NUM],
    poslim: MotorPosLimit,
    vellim: MotorVelLimit,
}
impl<MA, MB, MC> MotorHandler<MA, MB, MC>
where
    MA: StepperMotorController,
    MB: StepperMotorController,
    MC: StepperMotorController,
{
    pub fn new(
        motor_a: MA,
        motor_b: MB,
        motor_c: MC,
        poslim: MotorPosLimit,
        vellim: MotorVelLimit,
    ) -> MotorHandler<MA, MB, MC> {
        MotorHandler {
            motors: [
                GenericMotor::MotorA(motor_a),
                GenericMotor::MotorB(motor_b),
                GenericMotor::MotorC(motor_c),
            ],
            accel: [0.0f32; 3],
            poslim,
            vellim,
        }
    }
    pub fn get_motor_state(
        &mut self,
        telemetry_builder: &mut TelemetryBuilder,
    ) -> Result<[(KinState, MotorStatus); MOTOR_NUM], MotorHandlerError> {
        let mut state: [(KinState, MotorStatus); MOTOR_NUM] = Default::default();
        let motm2us = parameter_manager().get::<MotorM2Ustep>();
        for motor_idx in 0..MOTOR_NUM {
            let motstate = self.motors[motor_idx]
                .get_state()
                .map_err(|e| MotorHandlerError::MotorError(e, motor_idx))?;
            let mut kinstate: KinState = Default::default();
            kinstate.accel = self.accel[motor_idx];
            kinstate.speed = (motstate.velocity as f64 / motm2us as f64) as f32;
            kinstate.pos = (motstate.position as f64 / motm2us as f64) as f32;
            self.vellim
                .check(&mut kinstate.speed)
                .map_err(|e| MotorHandlerError::MotorVelocityLimitError(e, motor_idx))?;
            self.poslim
                .check(&mut kinstate.pos)
                .map_err(|e| MotorHandlerError::MotorPositionLimitError(e, motor_idx))?;
            let status = MotorStatus {
                limit_reached: motstate.limit_reached,
                position_reached: motstate.position_reached,
                velocity_reached: motstate.velocity_reached,
                standstill: motstate.standstill,
            };
            telemetry_builder.add_motor_state(motor_idx, &kinstate);
            state[motor_idx] = (kinstate, status)
        }
        Ok(state)
    }
    pub fn maybe_set_motor_input(
        &mut self,
        inputs: [Option<(KinState, ControlMode)>; MOTOR_NUM],
        telemetry_builder: &mut TelemetryBuilder,
    ) -> Result<(), MotorHandlerError> {
        let motm2us = parameter_manager().get::<MotorM2Ustep>();
        for motor_idx in 0..MOTOR_NUM {
            if let Some((state, mode)) = inputs[motor_idx] {
                telemetry_builder.add_motor_target(motor_idx, &state);
                let motor_mode = match mode {
                    ControlMode::Position => MotorMode::PositionCtrl,
                    ControlMode::Velocity => MotorMode::VelocityCtrl,
                };
                let input = MotorInput {
                    velocity: ((state.speed * motm2us) as i32)
                        .try_into()
                        .map_err(|_| MotorHandlerError::InputOverflow)?,
                    acceleration: ((state.accel * motm2us) as i32)
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

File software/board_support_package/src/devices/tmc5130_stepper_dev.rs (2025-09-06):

use crate::utils::error_wrapper::ErrorWrapper;
use device_traits::{
    MotorInput, MotorMode, MotorState, StepperDeviceError, StepperMotorController,
    StepperMotorPhase,
};
use tmc5130::reg::{DRV_STATUS, IOIN};
use tmc5130::{reg, Tmc5130};

pub struct TMC5130StepperDev<SPI, PIN> {
    dev_driver: Tmc5130<SPI>,
    limit_pin: PIN,
    map: reg::Map,
}

impl<SPI, PIN> TMC5130StepperDev<SPI, PIN>
where
    StepperDeviceError: From<ErrorWrapper<<SPI as embedded_hal::spi::ErrorType>::Error>>,
    SPI: embedded_hal::spi::SpiDevice,
    PIN: embedded_hal::digital::InputPin,
{
    fn get_error_from_drv_status(&mut self) -> Result<(), StepperDeviceError> {
        let (_status, read_drv_status) = self
            .dev_driver
            .read_register::<DRV_STATUS>()
            .map_err(|e| StepperDeviceError::from(ErrorWrapper(e)))?;
        if read_drv_status.s2ga() {
            Err(StepperDeviceError::ShortToGround(StepperMotorPhase::A))
        } else if read_drv_status.s2gb() {
            Err(StepperDeviceError::ShortToGround(StepperMotorPhase::B))
        } else if read_drv_status.ot() {
            Err(StepperDeviceError::OverTemperatureShutdown)
        } else if read_drv_status.olb() {
            Err(StepperDeviceError::OpenLoad(StepperMotorPhase::B))
        } else if read_drv_status.ola() {
            Err(StepperDeviceError::OpenLoad(StepperMotorPhase::A))
        } else {
            //Err(StepperDeviceError::OpenLoad(StepperMotorPhase::A))
            Ok(())
        }
    }

    fn get_error_from_spistatus(
        &mut self,
        status: reg::SPISTATUS,
    ) -> Result<(), StepperDeviceError> {
        if status.driver_error() {
            let (_status, read_drv_status) = self
                .dev_driver
                .read_register::<DRV_STATUS>()
                .map_err(|e| StepperDeviceError::from(ErrorWrapper(e)))?;
            if read_drv_status.s2ga() {
                Err(StepperDeviceError::ShortToGround(StepperMotorPhase::A))
            } else if read_drv_status.s2gb() {
                Err(StepperDeviceError::ShortToGround(StepperMotorPhase::B))
            } else if read_drv_status.ot() {
                Err(StepperDeviceError::OverTemperatureShutdown)
            } else if read_drv_status.ola() {
                Err(StepperDeviceError::OpenLoad(StepperMotorPhase::A))
            } else if read_drv_status.olb() {
                Err(StepperDeviceError::OpenLoad(StepperMotorPhase::B))
            } else {
                Ok(())
            }
        } else if status.reset_flag() {
            Ok(())
        } else {
            Ok(())
        }
    }
    fn clear_status_flags(&mut self) -> Result<(), StepperDeviceError> {
        let (_, _gstat) = self
            .dev_driver
            .read_register::<reg::GSTAT>()
            .map_err(|e| StepperDeviceError::from(ErrorWrapper(e)))?;
        let (_, _gstat) = self
            .dev_driver
            .read_register::<reg::GSTAT>()
            .map_err(|e| StepperDeviceError::from(ErrorWrapper(e)))?;
        Ok(())
    }
    fn self_test(&mut self) -> Result<(), StepperDeviceError> {
        const EXPECTED_IOIN_VERSION: u16 = 17;

        let (status, read_ioin) = self
            .dev_driver
            .read_register::<IOIN>()
            .map_err(|e| StepperDeviceError::from(ErrorWrapper(e)))?;
        self.get_error_from_spistatus(status)?;
        *self.map.ioin_mut() = read_ioin;
        if self.map.ioin().drv_enn_cfg6() {
            Err(StepperDeviceError::EnableError)
        } else if self.map.ioin().version() != EXPECTED_IOIN_VERSION {
            Err(StepperDeviceError::SelfTestVersionMismatch)
        } else {
            Ok(())
        }
    }
    fn initial_register_set(&mut self) -> Result<(), StepperDeviceError> {
        self.map.chopconf_mut().set_toff(3);
        self.map.chopconf_mut().set_hstrt(4);
        self.map.chopconf_mut().set_hend(1);
        self.map.chopconf_mut().set_tbl(2);
        self.map.chopconf_mut().set_chm(false);
        self.map.chopconf_mut().set_vsense(false);
        //set microstep resolution to 8 usteps
        self.map.chopconf_mut().set_mres(5);
        self.map.ihold_irun_mut().set_ihold(3);
        self.map.ihold_irun_mut().set_irun(20);
        self.map.ihold_irun_mut().set_ihold_delay(6);
        self.map.pwmconf_mut().set_pwm_autoscale(true);
        self.map.pwmconf_mut().set_pwm_ampl(200);
        self.map.pwmconf_mut().set_pwm_grad(1);
        self.map.pwmconf_mut().set_pwm_freq(0);
        self.map.gconf_mut().set_en_pwm_mode(true);
        self.map.gconf_mut().set_shaft(true);
        *self.map.tpowerdown_mut() = reg::TPOWERDOWN::from(10);
        *self.map.tpwmthrs_mut() = reg::TPWMTHRS::from(1000);
        *self.map.a1_mut() = reg::A1::from(0);
        *self.map.v1_mut() = reg::V1::from(0);
        *self.map.amax_mut() = reg::AMAX::from(500);
        *self.map.vmax_mut() = reg::VMAX::from(200000);
        *self.map.dmax_mut() = reg::DMAX::from(700);
        *self.map.d1_mut() = reg::D1::from(0);
        *self.map.vstop_mut() = reg::VSTOP::from(10);
        *self.map.vstart_mut() = reg::VSTART::from(0);
        *self.map.rampmode_mut() = reg::RAMPMODE::from(0);
        *self.map.xactual_mut() = reg::XACTUAL::from(0);
        *self.map.vactual_mut() = reg::VACTUAL::default();

        let mut actions = [
            tmc5130::Action::write(self.map.state(reg::Address::CHOPCONF)),
            tmc5130::Action::write(self.map.state(reg::Address::IHOLD_IRUN)),
            tmc5130::Action::write(self.map.state(reg::Address::TPOWERDOWN)),
            tmc5130::Action::write(self.map.state(reg::Address::GCONF)),
            tmc5130::Action::write(self.map.state(reg::Address::TPWMTHRS)),
            tmc5130::Action::write(self.map.state(reg::Address::PWMCONF)),
            tmc5130::Action::write(self.map.state(reg::Address::A1)),
            tmc5130::Action::write(self.map.state(reg::Address::V1)),
            tmc5130::Action::write(self.map.state(reg::Address::AMAX)),
            tmc5130::Action::write(self.map.state(reg::Address::VMAX)),
            tmc5130::Action::write(self.map.state(reg::Address::DMAX)),
            tmc5130::Action::write(self.map.state(reg::Address::D1)),
            tmc5130::Action::write(self.map.state(reg::Address::VSTOP)),
            tmc5130::Action::write(self.map.state(reg::Address::VSTART)),
            tmc5130::Action::write(self.map.state(reg::Address::RAMPMODE)),
            tmc5130::Action::write(self.map.state(reg::Address::XACTUAL)),
        ];
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

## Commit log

2023-11-02 schematics almost ready for plate
    [capacitive_plate_pcb.kicad_pcb, capacitive_plate_pcb.kicad_sch]
2023-11-07 almost done layout
    [capacitive_plate_pcb.kicad_pcb, capacitive_plate_pcb.kicad_sch]
2023-11-13 R01 plate pcb
    [capacitive_plate_pcb.kicad_pcb, capacitive_plate_pcb.kicad_sch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]
2024-02-09 inductive test pcb manufactured
    [inductive_plate_test.kicad_pcb, inductive_plate_test.kicad_sch]
2024-09-05 renaming bsp_traits to device_traits
2024-09-05 resistive plate pcb R01
    [resistive_plate.kicad_pcb, resistive_plate.kicad_sch]
2024-09-05 post mgf commit
    [resistive_plate.kicad_pcb, resistive_plate.kicad_sch]
2024-11-22 central control board R01 production
    [central_control_board.kicad_pcb, central_control_board.kicad_sch, motor_drive_a.kicad_sch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]
2024-12-17 enable fix + test motion
    [io_manager.rs, lib.rs, menu_handler.rs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]
2025-02-23 mfg version of reduced resistive board
    [reduced_resistive_board.kicad_pcb, reduced_resistive_board.kicad_sch]
2025-07-12 add Flush buffer button to telemetry (#6)
2025-07-12 Fix my own mess
    [main.rs]
2025-07-16 fix plate direction
2025-09-06 Remove all traces of defmt
